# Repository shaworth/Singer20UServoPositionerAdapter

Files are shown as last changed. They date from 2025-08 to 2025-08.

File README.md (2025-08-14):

# Singer 20u33 Servo Position Sensor Adapter
Everything you need to retrofit your Singer 20u33 (and clones) servo upgrade with a needle position sensor.

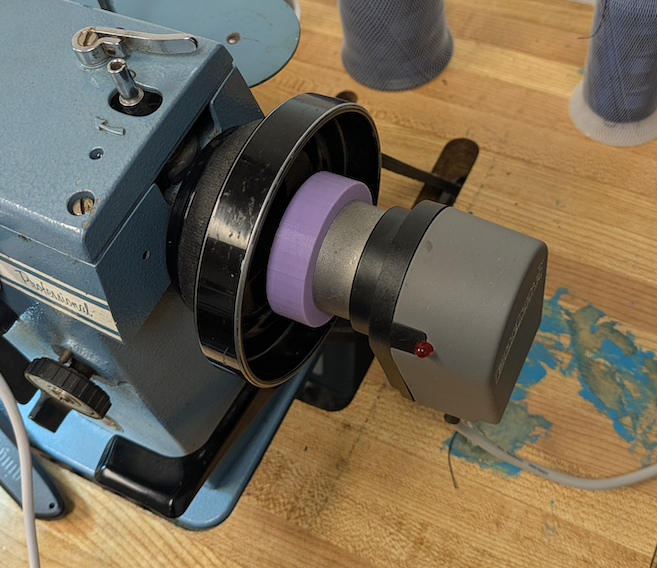
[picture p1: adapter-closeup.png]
Adapter


## Overview
The Singer 20U33 / 20-33 and clones are industrial sewing machines that utilize a hand clutch at the end of the main shaft to disengate / engage the sewing mechanism from the bobbin winder.  This allows the operator to wind bobbins without running the sewing mechanism.  However, servo needle position sensors expect the main shaft to have an exposed center tap to screw the adapter into.

My solution is to fit a 3D printed adapter over the hand clutch, that the position sensor can screw into.  A strong magnet holds everything in place.

### But 'Why?", Servos and Industrial Clutch Motors
Industrial sewing machines have historically used powerful AC motors spinning at all times, and a foot clutch to engage the drive pully.  This arrangement is fantastic for highly skilled operators.  The amount of on-demand power is amazing, and with skill the speed can be controled with high precision.

For the rest of us, these beasts (I can barely lift the motor it is so heavy) are intimidating, noisy and difficult to control.

Servos on the other hand work a lot like a domestic foot pedal.  Press the pedal and the motor spins.  However, if a needel positioner is installed two other features are available.  
 1. By default, if the sensor is attached, the servo is configured to always stop with the needle in the DOWN position.  This is handy for making tight turns.  Stop sewing, lift the foot, turn the material, lower the foot and continue sewing.  The needle keeps the work item aligned, and thread tension is preserved.  
 2. By default the servo is configured to bring the needle to the UP position by pressing on the heel of the foot pedal.  Stop the machine, press your heel against the bottom of the pedel and the needle lifts out of the way and into the thread release position.

Both of these operations are highly repeatable and reliable.

If these two capabilites don't sound like a big deal you are either not the target audiance (you are likely a professional), or you haven't used an industrial machine with a servo yet.  Because once you do, boy-howdy, there is no going back.

I researched off-the-shelf adapters to mounting a position sensor without any luck.  I found a refrence to a discontinued adapter that cost about $90 USD.  But the reference was three years old and the part is unavailable.  So I designed my own 3D printed solution.  Sharing is caring, which brings us here.  Oh, look at the [BOM](bom.md), this adapter costs less than $5.00 USD (2025).

Enjoy!

## Requirements
1. Inexpensive.
2. Easy.
3. Non-destructive.  Don't replace or modify any part of the machine.
4. The position sensor expects a certain shape and size flange to attach to.  The flange must be mounted on and synchronized with the main shaft.

## Solution

The solution involves a 3D printed flange (comprised of two sub-assemblies) and a 130lb magnet that holds the flange on the existing handwheel.

## Instructions

Print the two pieces of the flange (no supports necessary).

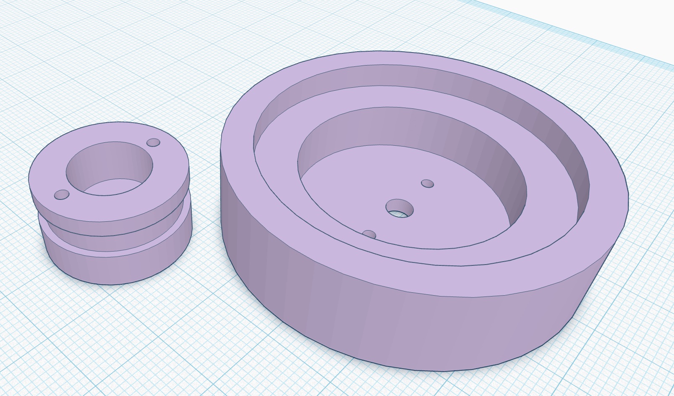
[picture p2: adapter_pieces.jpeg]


Place the Magnet and the Screw in the large half of the flange.

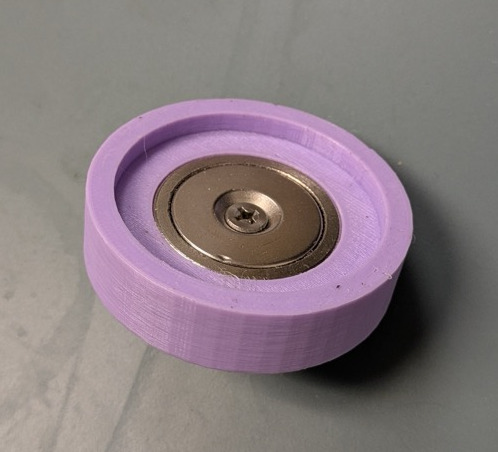
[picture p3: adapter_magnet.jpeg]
Magnet


Flip the large half of the flange over, attach the small half of the flange with the whiz nut.  Insert the two alignment pins (I used a couple of small nails that I cut to length).

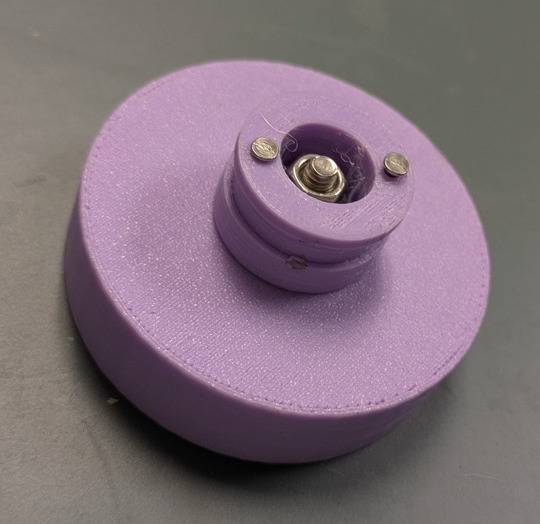
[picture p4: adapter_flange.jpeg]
Flange


Attach the sensor to the flange

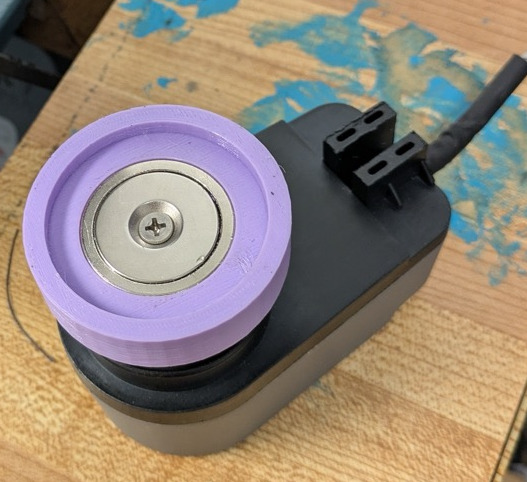
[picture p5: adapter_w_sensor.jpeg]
Sensor


Finally, snap (you have no choice, it will SNAP!) the assembly onto the handwheel.

## Calibrate the sensor position

The goal here is to manually turn the machine until the needle is in the UP position.  Then, turn the flange (you have to hold the handwheel, the magnet has a strong grip) until the LED on the sensor activates.  

If that doen't work (no LED for instance), sew a stitch, and adjust the flange position based on how far off it is.  Usually you can zero in with only a couple of tries.

That's it.

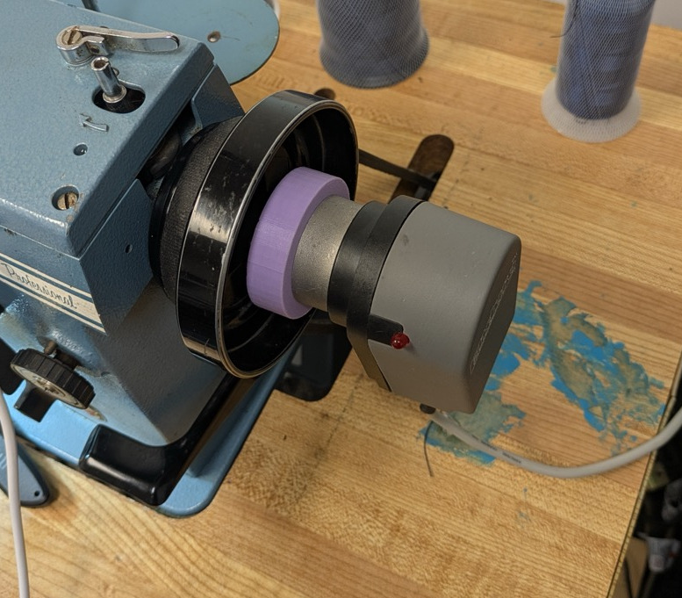
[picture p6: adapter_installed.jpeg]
Installed


Released under the [Creative Commons non-commercial license](License.txt)

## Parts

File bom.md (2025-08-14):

# Bill of Materials

| Description | Qty | Cost, 2025 USD |
|---|-----|---|
| 4mm x 20mm screw | 1 | $0.89 |
| 4mm Whiz Nut | 1 | $0.45 | 
| brads (aka wire nails) | 2 | $0.01 |
| [130 Lb Magnet](https://www.amazon.com/Neosmuk-Neodymium-Countersunk-Stainless-Rack-Pack/dp/B08HMGMXSH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) | 1 | $1.70 |

Total: ~ $4.00

In addition you will need access to a 3D printer, or use an on-demand printing service.

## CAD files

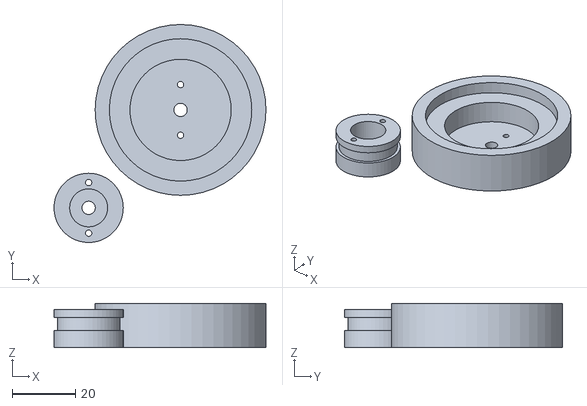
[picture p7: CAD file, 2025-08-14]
22U33 Handwheel Needle Positioner.stl
67.0 x 68.9 x 14.0

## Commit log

2025-08-14 Create bom.md
    Initial BOM
2025-08-14 Update bom.md
    fixed syntax error
2025-08-14 Update bom.md
    Formatting improvements
2025-08-14 Update bom.md
    Added link to magnets
2025-08-14 Add files via upload
    Photos and gcode and stl
    [22U33 Handwheel Needle Positioner.stl]
2025-08-14 Add files via upload
    Added STL preview
